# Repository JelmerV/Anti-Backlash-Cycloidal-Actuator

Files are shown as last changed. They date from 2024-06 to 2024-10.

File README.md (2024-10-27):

# MSc Thesis - Cost-Effective and Torque-Dense Cycloidal Actuator with Anti-Backlash Mechanisms

Accompaning files for the thesis work "Anti-Backlash Mechanisms for Cost-Effective Cycloidal Drive Robotic Actuators: Design and Evaluation"

Results - Test scripts - CAD source - Step files - Documentation - Diagrams - Photos

## Abstract

3D-printing is a promising method for cost-effective actuator designs, but it often results in less precise tolerances, leading to increased play.
In this work, we propose two novel anti-backlash mechanisms for cycloidal reducers. One uses a conically shaped cycloidal disk, and the other uses a split non-pinwheel design. Both were integrated into a compact actuator design. Two prototypes were manufactured and extensively tested in comparison to a baseline model. Experimental results show that the proposed mechanisms reduce play at the cost of increased friction. Both mechanisms utilize an adjustable preload that can be configured for the intended application based on the trade-off between play and friction.
Furthermore, the designed actuator demonstrates performance that is competitive with recent works. Using 3D-printed components proves to be a viable manufacturing method for cost-efficient designs.

## Actuator design

Baseline section views

<p float="left">
  Prototype parts
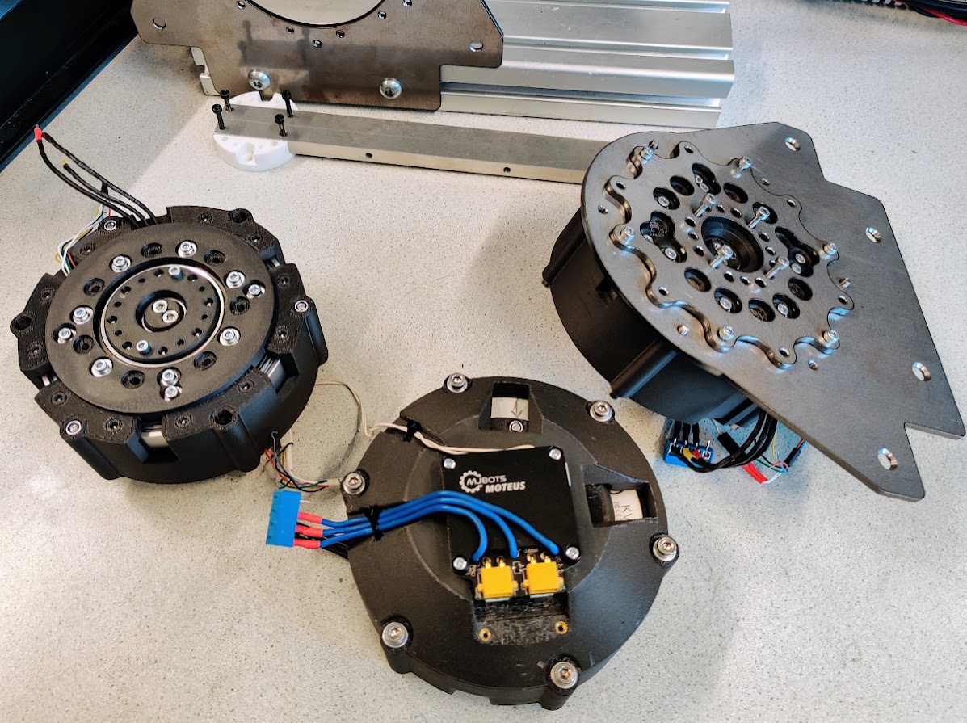
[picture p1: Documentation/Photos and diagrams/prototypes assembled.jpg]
Three assembled prototypes and mounting and locking plates
  
</p>

## Anti-Backlash mechanism

<p float="left">
    Split Non-pinwheel mechanism - modified parts
    Conic Cycloidal disk mechanism - modified parts
</p>

## File overview

`Agendas` All meeting agendas

`CAD Export` Exported CAD files, such as STEP files of the assemblies and individuald STL or STEP parts for 3D-printing

`CAD Source` SOLIDWORKS files of all components for easy modification

`CAD Source/test setup` SOLIDWORKS files for parts related to the tests and test setup

`CAD Source/off-the-shelf` SOLIDWORKS files for sourced parts, such as bearings and hardware

`Cycloid and Non-Pinwheel Profile Generation` Jupyter notebook file with scripts for the generation of cycloidal and non-pinwheel profiles. Included function to export (part of) the profile to DXF.

`Documentation` Files for some of the tables and comparisons of the paper

`Documentation/diagrams` SVG files of all diagrams and annotated images

`Documentation/CAD Section Views` Screenshots of the CAD design

`Documentation/Cad animations` Videos of the motions and exploded views of the CAD design

`Documentation/All photos and videos` All pictures and photos from the timeline of the project. All files are timestamped, so recorded tests can e matched by video and raw data

`Test Scripts` More details about these scripts in [corresponding README](<Test Scripts/README.md>)

`Test Scripts/test_data` Resulting test data, all files have timestamps and short descriptions in the name. All of the used data is aready added in the analysing notebook files

`Test Scripts/figures` Resulting plots as SVG files from the analysis notebooks

## License

Shield: [][cc-by-sa]

This work is licensed under a
[Creative Commons Attribution-ShareAlike 4.0 International License][cc-by-sa].

[][cc-by-sa]

[cc-by-sa]: http://creativecommons.org/licenses/by-sa/4.0/
[cc-by-sa-image]: https://licensebuttons.net/l/by-sa/4.0/88x31.png
[cc-by-sa-shield]: https://img.shields.io/badge/License-CC%20BY--SA%204.0-lightgrey.svg

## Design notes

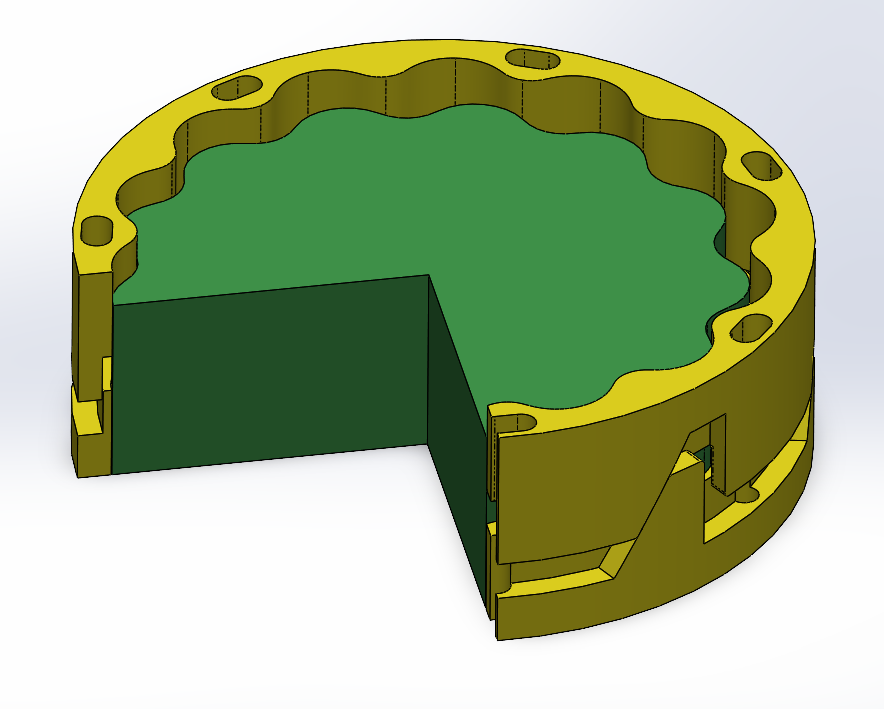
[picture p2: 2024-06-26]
Documentation/Preloading Concept Exploration/split pinwheel.png

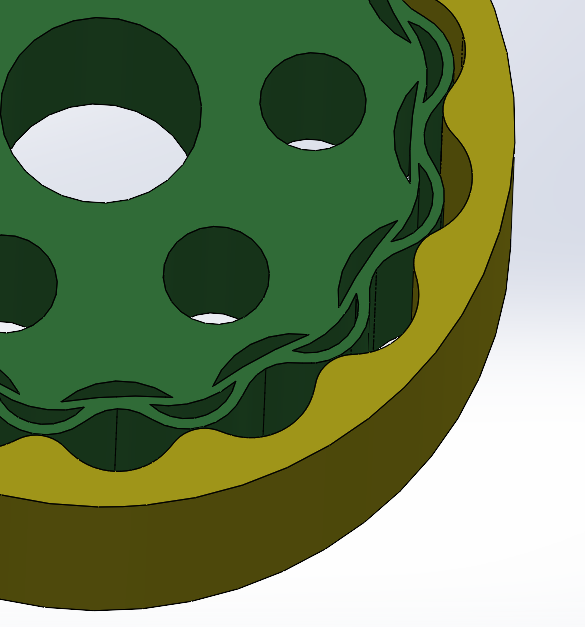
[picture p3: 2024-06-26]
Documentation/Preloading Concept Exploration/spring teeth disk close-up.png

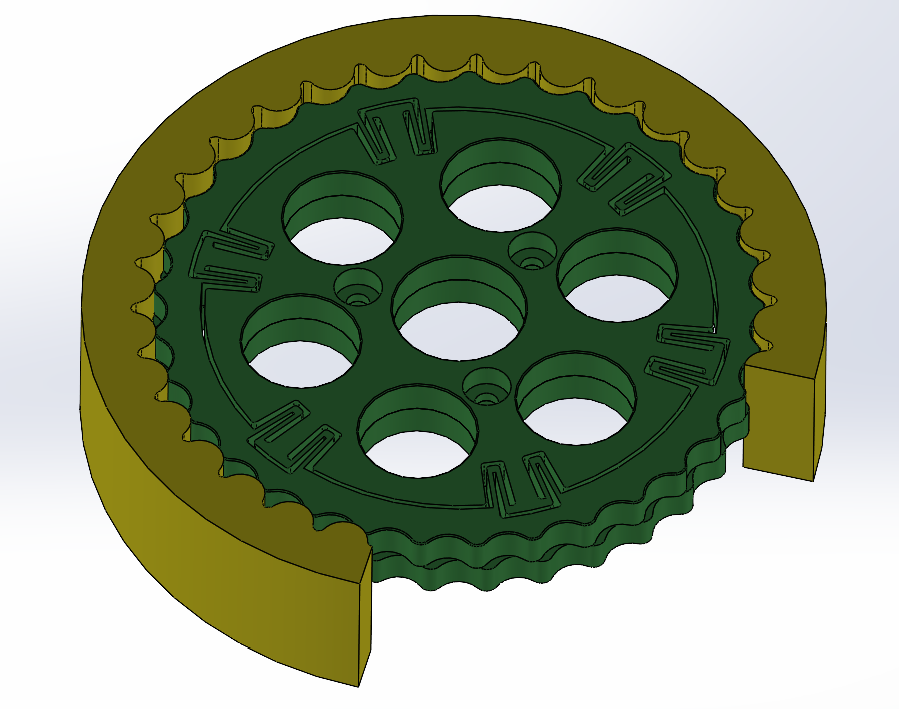
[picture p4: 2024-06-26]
Documentation/Preloading Concept Exploration/split disk flexure - sectioned.png

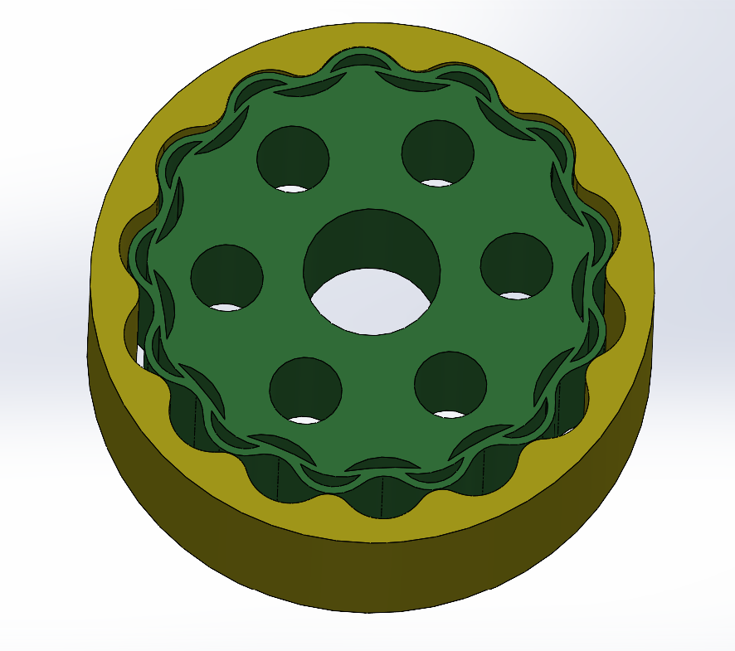
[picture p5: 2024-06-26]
Documentation/Preloading Concept Exploration/spring teeth disk.png

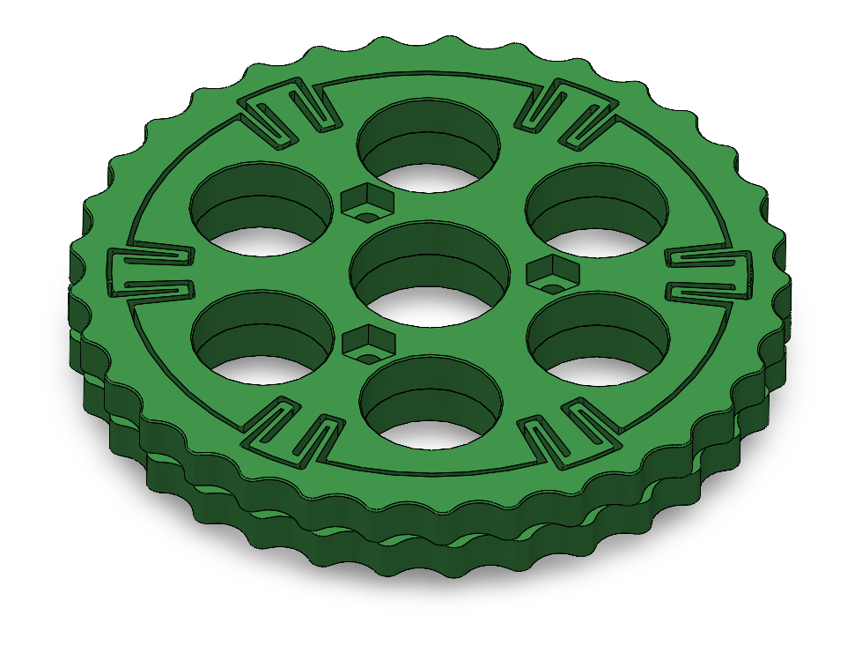
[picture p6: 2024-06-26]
Documentation/Preloading Concept Exploration/split disk flexures.png

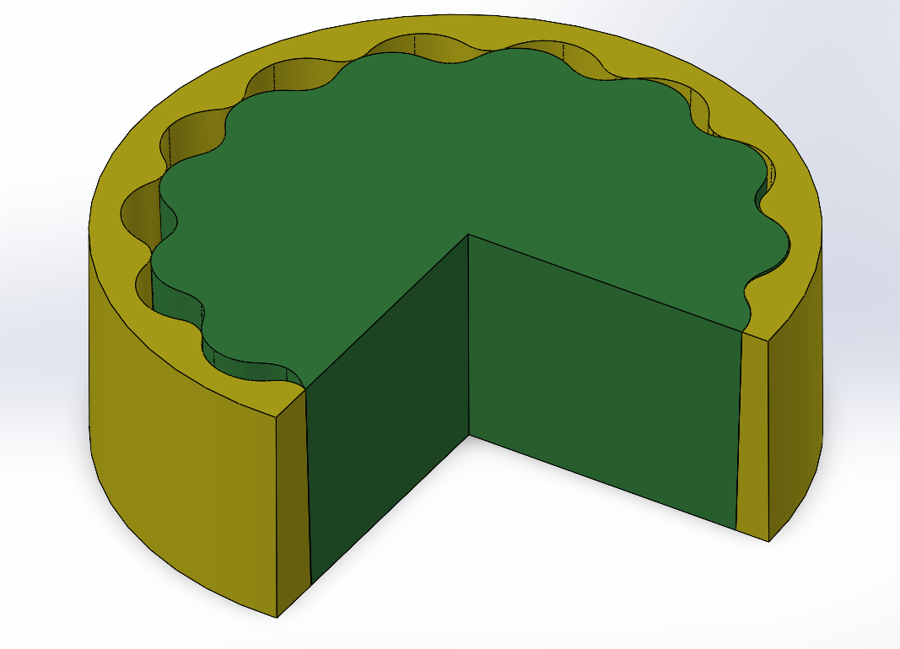
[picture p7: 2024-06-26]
Documentation/Preloading Concept Exploration/conic - sectioned.png

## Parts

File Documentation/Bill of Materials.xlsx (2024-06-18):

Kugellager express
Item | price | amount | total | link | Notes
6710 (50x62x6) | 9.95 | 10 | 99.5 | https://www.kugellager-express.de/deep-groove-ball-bearing-6710-61710-2rs-50x62x6-mm
6803 (17x26x5) | 1.39 | 5 | 6.95 | https://www.kugellager-express.de/deep-groove-ball-bearing-6803-61803-2rs-17x26x5-mm
6806 (30x42x7 | 2.89 | 4 | 11.56 | https://www.kugellager-express.de/deep-groove-ball-bearing-6806-61806-2rs-30x42x7-mm
HK 0509 | 0.71 | 100 | 71 | https://www.kugellager-express.de/drawn-cup-needle-roller-bearing-hk0509-open-hk0509-5x9x9-mm
HK 1522 | 2.84 | 4 | 11.36 | https://www.kugellager-express.de/drawn-cup-needle-roller-bearing-hk1522-open-hk1522-15x21x22-mm
IR 12x15x22.5 | 3.28 | 4 | 13.12 | https://www.kugellager-express.de/inner-ring-ir12x15x22-5-12x15x22-5-mm
total |  |  | 213.49
 |  |  |  |  |  | per actuator | total
DIN912 - M2.5x10 |  |  |  | at ram stock |  | 4 | 16
DIN912 - M2.5x35 |  |  |  |  |  | 7 | 14 | https://www.conrad.nl/nl/p/toolcraft-to-5358816-cilinderschroeven-m2-5-35-mm-sleuf-rvs-a2-1000-stuk-s-1786272.html | https://www.rwproducts.nl/din-912-cilinderschroef-binnenzeskant-rvs-a4-m2-5x35 | https://www.fabory.com/nl/cilinderschroef-met-binnenzeskant-din-912-roestvaststaal-%28rvs%29-a4-70-m2%2C5x35/p/55050025035
DIN912 - M3x6 |  |  |  | at ram stock |  | 10 | 40
DIN912 - M3x8 |  |  |  | at ram stock |  | 8 | 32
DIN912 - M3x12 |  |  |  | at ram stock |  | 7 | 28
DIN912 - M4x50 |  |  |  |  |  | 8 | 32
Countersink M4x10 |  |  |  |  |  | 10 | 40
Locknut M2.5 |  |  |  | at ram stock |  | 7 | 14
Locknut M3 |  |  |  | at ram stock |  | 26 | 104
Locknut M4 |  |  |  |  |  | 14 | 56
Washer M3 |  |  |  | at ram stock |  | 7 | 28
Washer M4 |  |  |  |  |  |  | 0
Large Washer M3 |  |  |  |  |  | 24 | 96
Large Washer M4 |  |  |  |  |  |  | 0
Fabory
DIN7979 Parallel pin with internal thread 5x45 (part nr. 39090.050.045) |  | 50 | 87 | https://www.fabory.com/nl/cilindrische-pen-met-binnendraad%2c-gehard%2c-geslepen-din-7979-d-staal-60%c2%b12hrc-blank-5x45mm/p/39090050045 | minimum quantity of 50. Need 40
AlcoMex Springs
Golfring W61460 | 3.15 | 5 | 15.75 | https://webshop.alcomex.nl/golfring-w61460
Schotelveer S22000 | 0.6 | 50 | 30 | https://webshop.alcomex.nl/schotelveer-8x3-2x0-3-s22000
total |  |  | 45.75
TinyTronics
Heat set inserts M2.5x5 (20pcs pack) | 2.5 | 1 | 2.5 | https://www.tinytronics.nl/en/tools-and-mounting/installation-and-mounting-material/threaded-inserts/threaded-insert-m2.5-5.0mm-20-pieces
Heat set inserts M3x5.7 (20pcs pack) | 2.75 | 2 | 5.5 | https://www.tinytronics.nl/en/tools-and-mounting/installation-and-mounting-material/threaded-inserts/threaded-insert-m3-5.7mm-20-pieces
Heat set inserts M4x5.8 (20pcs pack) | 3 | 1 | 3 | https://www.tinytronics.nl/en/tools-and-mounting/installation-and-mounting-material/threaded-inserts/threaded-insert-m4-5.8mm-20-pieces
Glue (metal to plastic)

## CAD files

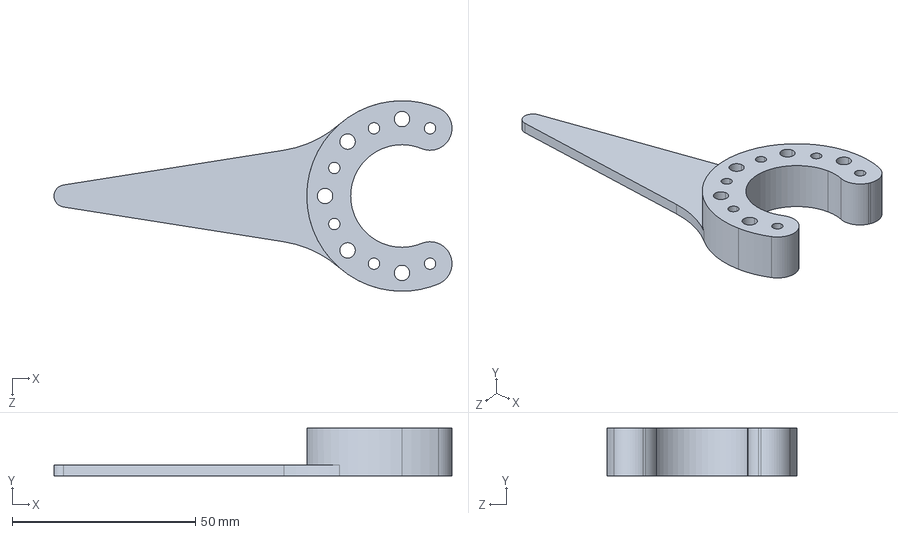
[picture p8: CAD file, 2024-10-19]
CAD Export/Output pointer.STEP
108.6 x 13.0 x 52.0 mm

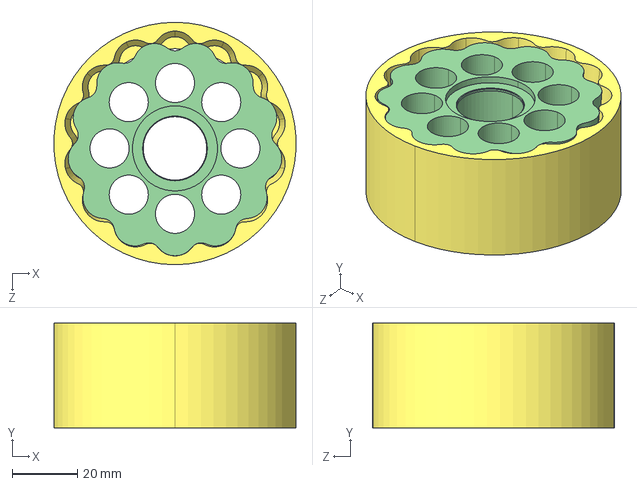
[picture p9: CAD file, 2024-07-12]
CAD Export/reducer parts V1.6/Cycloid Imported - Conic v1.6.STEP
74.0 x 32.0 x 74.1 mm

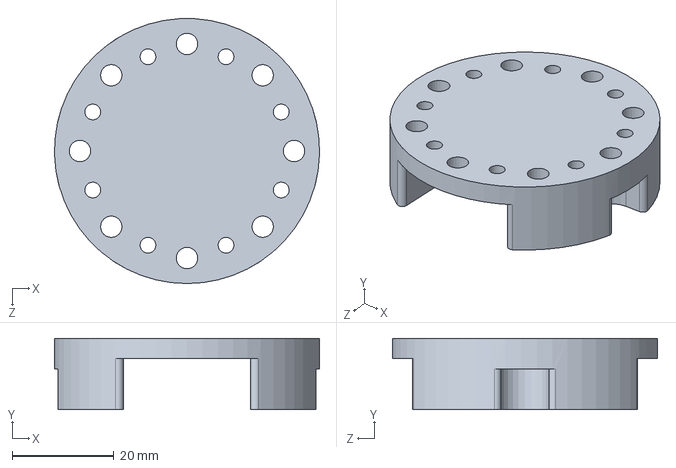
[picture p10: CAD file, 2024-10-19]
CAD Source/test setup/pendulum bar spacer.SLDPRT
52.0 x 14.0 x 52.0 mm

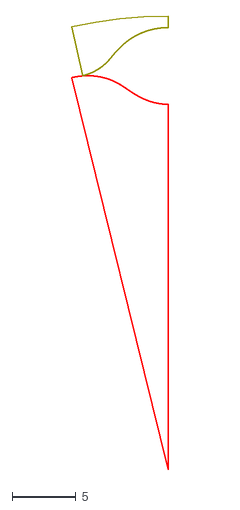
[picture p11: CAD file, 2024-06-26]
Cycloid and Non-Pinwheel Profile Generation/cycloid_N14_R34_Rr3.9_E1.5.dxf
7.57 x 35.5

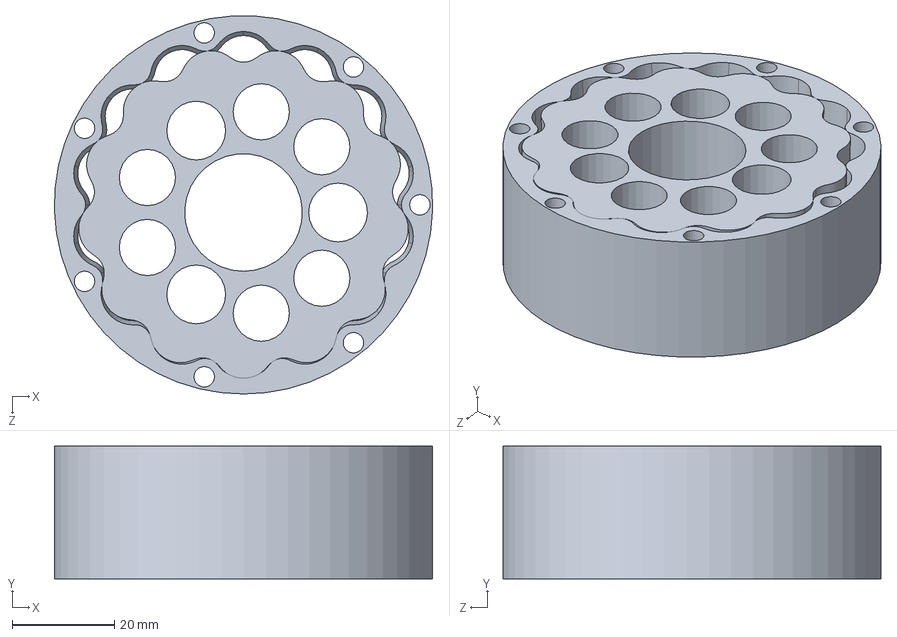
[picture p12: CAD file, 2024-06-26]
Documentation/Preloading Concept Exploration/conic cycloid import.SLDPRT
74.0 x 26.0 x 73.9 mm

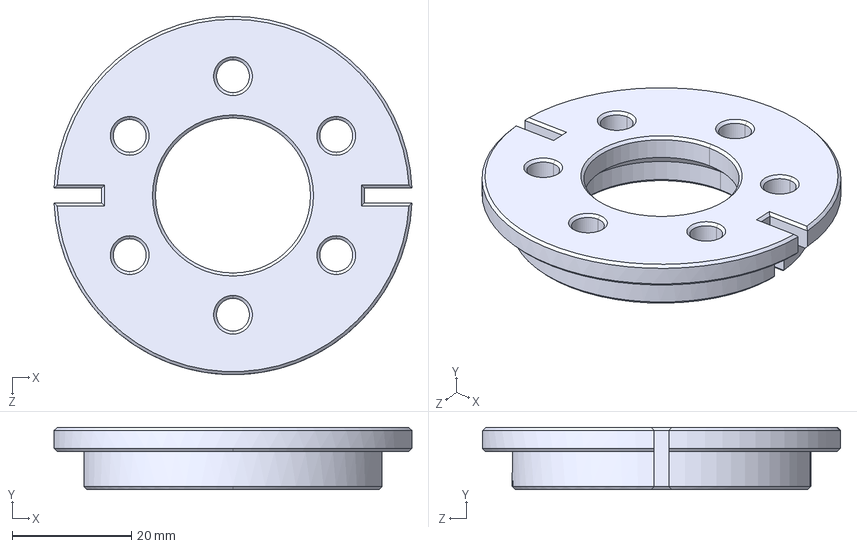
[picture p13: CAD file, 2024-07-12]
CAD Export/Rotor positioning tool.STEP
60.0 x 10.4 x 60.1 mm

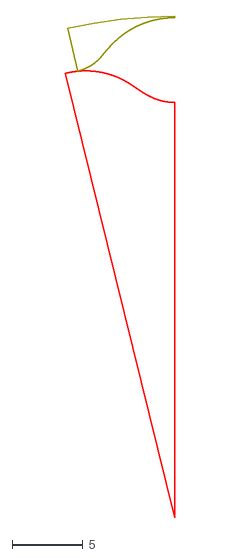
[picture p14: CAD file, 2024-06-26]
Cycloid and Non-Pinwheel Profile Generation/cycloid_N14_R34_Rr3.1_E1.5.dxf
7.75 x 35.5

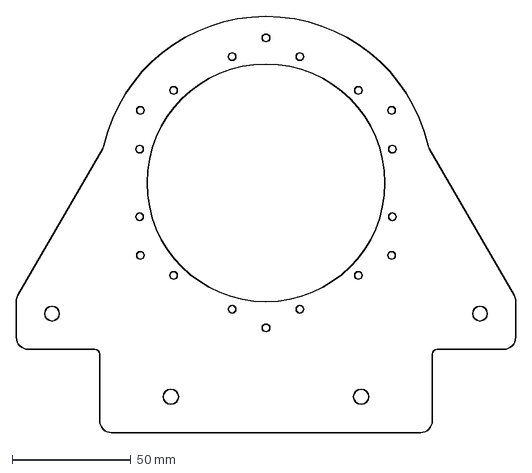
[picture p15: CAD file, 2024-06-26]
CAD Export/Actuator Mounting Plate.DXF
210.0 x 175.0 mm

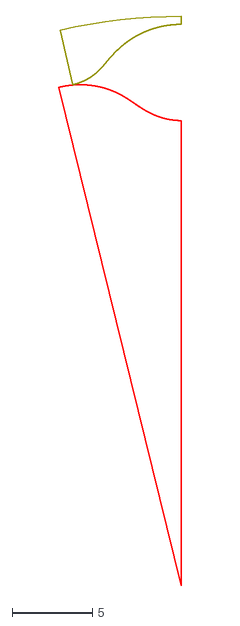
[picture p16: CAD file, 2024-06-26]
Cycloid and Non-Pinwheel Profile Generation/cycloid_N14_R34_Rr3.5_E1.5.dxf
7.66 x 35.5

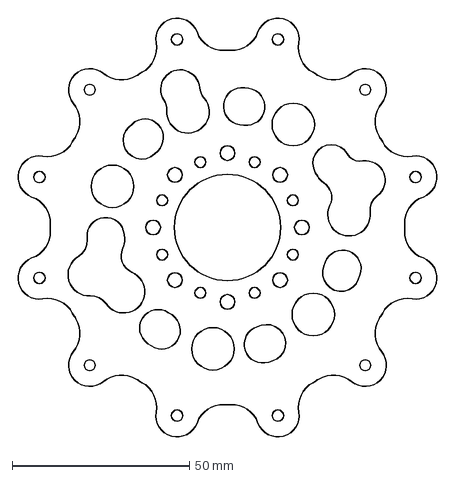
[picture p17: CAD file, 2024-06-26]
CAD Export/Output Fixing Plate.DXF
119.4 x 119.4 mm

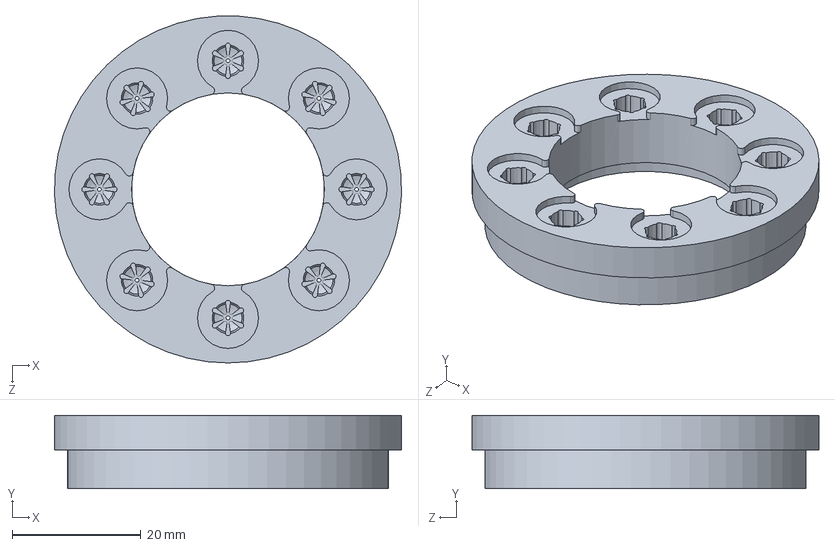
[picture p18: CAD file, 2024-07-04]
CAD source/Output Stiffener.SLDPRT
54.0 x 11.4 x 54.0 mm

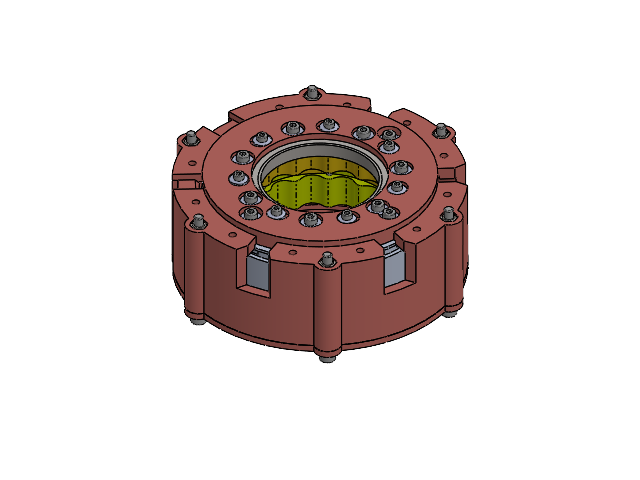
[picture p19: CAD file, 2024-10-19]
CAD source/Housing and Fixed parts.SLDASM
Housing base
Housing cap
RO100 - windings
RO100 - stator
RO100 - windings bottom
Cycloid Imported - Split Pinwheel
Ball Bearing Deep Groove
Moteus-r411-mechanical
Plain Washers x 16
Hex Socket Screw (DIN912) x 20
Locknut (DIN985) x 17
Heat Set Insert x 13
cable strain relief

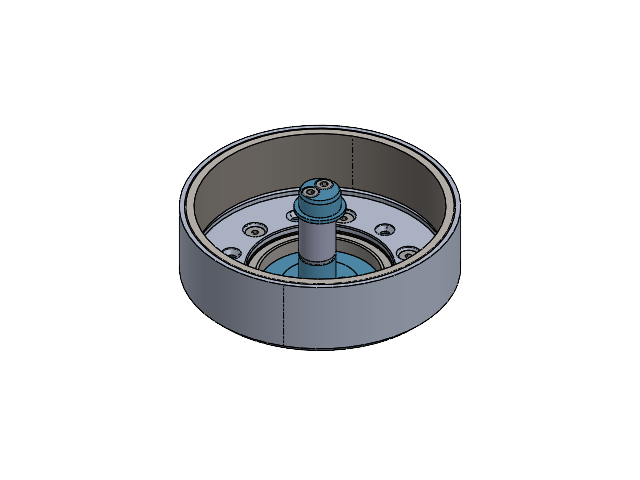
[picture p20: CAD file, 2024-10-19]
CAD source/Eccentric Shaft assem.SLDASM
Eccentric Shaft x 3
RO100 - rotor
RO100 - magnets
Ball Bearing Deep Groove x 2
Hex Socket Screw (DIN912) x 8
Shaft Liner IR_12x15x22.5
Moteus Diametric Sense Magnet
Locknut (DIN985) x 18
Preloading Ring x 2
Wave Disc Spring x 2
Hex Socket Screw Countersunk (DIN7991) x 6

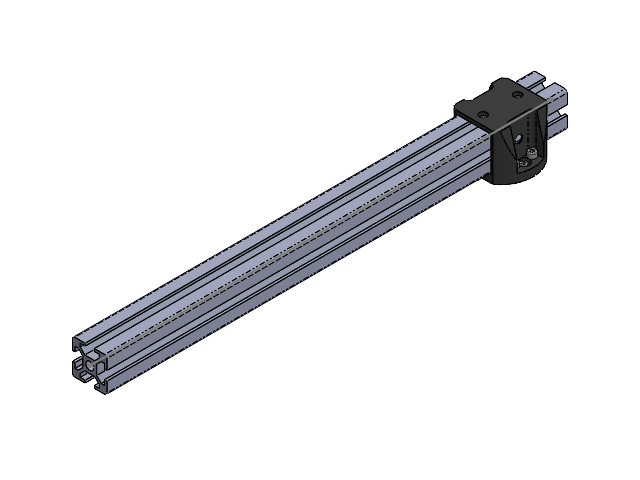
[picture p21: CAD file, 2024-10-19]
CAD source/Test setup/Pendulum.SLDASM
Output extrusion mount
Hex Socket Screw (DIN912) x 8
Plain Washers x 4
pendulum link

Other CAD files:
CAD source/Output Structure.SLDASM
CAD source/Cycloidal Disk assem.SLDASM
CAD source/Test setup/test base.SLDASM
CAD Source/test setup/Output pointer.SLDPRT
CAD Export/Output pointer.STL
CAD source/Eccentric Shaft.SLDPRT
CAD source/Housing base.SLDPRT
CAD source/Housing cap.SLDPRT
CAD source/Output Ring.SLDPRT
CAD source/Preloading Ring.SLDPRT
CAD source/Test setup/ATI Mini40 mount.SLDPRT
CAD source/Test setup/Actuator Mount print.SLDPRT
CAD source/Test setup/Actuator Mounting Plate.SLDPRT
CAD source/Test setup/Ati Mini40.SLDPRT
CAD source/Test setup/Output extrusion mount.SLDPRT
CAD source/Test setup/motor testing Shaft.SLDPRT
CAD source/Test setup/output fixing plate.SLDPRT
CAD source/Test setup/pendulum link.SLDPRT
CAD source/Test setup/testbed.SLDPRT
CAD source/cable strain relief.SLDPRT
CAD source/off-the-shelf/3030 corner bracket.SLDPRT
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

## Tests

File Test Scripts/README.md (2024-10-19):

# Script details:

## Test scripts:

These scripts require the moteus python library, installed via `pip3 install moteus`. See the [python reference](https://github.com/mjbots/moteus/blob/main/lib/python/README.md) and the  [full Moteus reference](https://github.com/mjbots/moteus/blob/main/docs/reference.md) for details.

`actuator.py` Shared abstraction layer for the moteus motor controller using the USB to canFD interface. Used by all other test scripts

`record_max_torque.py` torque ramps with configurable duration and peak

`record_speedramp.py` Speed ramp with configurable duration and peak

`record_torque_constant.py` Torque ramp in combination with a mini40 loadcell (untested)

`record_torqueramp.py` Torque ramps for play and stiffness. multiple repetations at 2 different peaks. Used for play and stiffness estimation

`record_trajectory.py` For a trajectory of postions with configurable speed limit. Repeats trajectory at increasing accelerations.

`record-run-in.py`  Run actuator in alternating directions indefinetly while saving CSV data.

## Data processing scripts

These files are jupyter notebook files requiring the jupyter python library, or can be opened using vs-code. Furthermore, they require some libraries installed by `pip install numpy matplotlib pandas`

`analyse_anti-backlash.ipynb` jupyter notebook for the play, stiffness, and friction tests and all resulting plots. Saved plots as SVG are the ones used in the the paper.

`analyse_performance.ipynb` jupyter notebook for the maximum torque and velocity tests and plots, as well as the pendulum trajectory tracking tests and corresponding plots

## Directory

`./test_data` Resulting test data, all files have timestamps and short descriptions in the name. All of the used data is aready added in the analysing notebook files

`./figures` Resulting plots as SVG files from the analysis notebooks

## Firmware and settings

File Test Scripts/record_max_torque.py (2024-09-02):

'''
Do a slow torque ramp towards a small position change. Used to estimate internal play and stiffness
'''

import time, datetime
import math

import numpy as np
import pandas as pd
import matplotlib.pyplot as plt
import threading

import asyncio
from actuator import Actuator

abs_start_time = time.monotonic_ns()
e_stop = False

async def do_torque_ramp(actuator: Actuator, duration, max_torque):
    # ramp up till max torque in either direction 
    ramp_duration = duration/2

    states = []
    succes = True

    try:
        print(f'Ramping to {max_torque} Nm in {ramp_duration} seconds.', end=' ', flush=True)
        start_time = time.monotonic_ns()
        while not e_stop:
            pct_done = (time.monotonic_ns() - start_time) / (ramp_duration*1e9)
            if pct_done > 1.0:
                break
            torque = max_torque * pct_done
            result = await actuator.set_position(feedforward_torque=torque, kp_scale=0.0, kd_scale=0.0, velocity_limit=0.5)
            states.append(actuator.state_to_dict(result, time.monotonic_ns()))
            await asyncio.sleep(0.001)
            
        if states[-1]['FAULT'] != 0:
            print(f'fault code: {states[-1]["FAULT"]}, STOPPING')
            raise Exception('Fault detected')

        #ramp down torque
        print(f'\tand back down', end=' ', flush=True)
        start_time = time.monotonic_ns()
        while not e_stop:
            pct_done = (time.monotonic_ns() - start_time) / (ramp_duration*1e9)
            if pct_done > 1.0:
                break
            torque = max_torque * (1-pct_done)
            result = await actuator.set_position(feedforward_torque=torque, kp_scale=0.0, kd_scale=0.0, velocity_limit=0.02)
            states.append(actuator.state_to_dict(result, time.monotonic_ns()))
            await asyncio.sleep(0.001)

    except Exception as e:
        print(f'torqueramp failed. Error: {e}')
        succes = False

    finally:
        if e_stop:
            print(f'Emergency stop detected, stopping motor')
            succes = False
        print(f'\tDone. stopping motor')
        # await actuator.m.set_stop()
            
        return succes, states
    

def torque_ramp_test(actuator: Actuator, test_duration, max_torque):
    ramp_duration = test_duration/2
    pos_succes, pos_states = asyncio.run(do_torque_ramp(actuator, ramp_duration, max_torque))
    test_df = pd.DataFrame(pos_states)
    if pos_succes:
        neg_succes, neg_states = asyncio.run(do_torque_ramp(actuator, ramp_duration, -max_torque))
        test_df = pd.concat([test_df, pd.DataFrame(neg_states)])
    
    if not pos_succes or not neg_succes:
        asyncio.run(actuator.m.set_stop())
        asyncio.run(actuator.set_position_bounds('nan', 'nan'))

        timestamp = datetime.datetime.now().strftime('%Y-%m-%d__%H-%M-%S')
        filename = f'test_data/{timestamp}__torquerampfailed__{test_name}.csv'
        test_df.to_csv(filename, index=False)

        print(f'Ramp failed, still saved data to {filename}')
        test_df.plot(x='TIME', y='TORQUE')
        plt.show()
        exit()
        
    # test_df['TORQUE_smooth'] = test_df['TORQUE'].rolling(window=20, center=True).mean()
    return test_df


def e_stop_detector():
    global e_stop
    while True:
        inp = input('type q to stop: ')
        if inp == 'q':
            e_stop = True
            break
        time.sleep(0.05)
    


if __name__ == '__main__':
    STIFFNESS_TEST_TORQUE = 90.0          # Nm at output
    STIFFNESS_TEST_DURATION = 8.0
    STIFFNESS_TEST_REPETITIONS = 2

    # STORED_DATA = ['POSITION', 'TORQUE', 'CONTROL_TORQUE', 'Q_CURRENT', 'FAULT', 
    STORED_DATA = [ 'POSITION', 'TORQUE', 'CONTROL_TORQUE', 'Q_CURRENT',
                    'FAULT', 'TRAJECTORY_COMPLETE',
                    'TEMPERATURE', 'MOTOR_TEMPERATURE',
    ]


    print('\nStarting torque ramp test')
    print(f'torque test: {STIFFNESS_TEST_TORQUE}Nm, {STIFFNESS_TEST_DURATION}s, {STIFFNESS_TEST_REPETITIONS} repetitions')
    print('')
    test_name = input('Enter test name: ')

    if test_name == '':
        print('No test name given, exiting')
        exit()


    # initialize actuator
    actuator = Actuator(actuator_id=1, stored_data=STORED_DATA)

    # set position to zero
    asyncio.run(actuator.m.set_output_nearest(position=0.0))

    #for safety, configure motion limits
    MAX_DEVIATION = 0.3    # measured in output revolutions    
    result = asyncio.run(actuator.set_position())
    asyncio.run(actuator.m.set_stop())
    cur_pos = actuator.state_to_dict(result)['POSITION']
    print(f'Current position: {cur_pos}, setting bounds to {cur_pos-MAX_DEVIATION} to {cur_pos+MAX_DEVIATION}')
    asyncio.run(actuator.set_position_bounds(cur_pos-MAX_DEVIATION, cur_pos+MAX_DEVIATION))


    #start emergency stop
    e_stop_thread = threading.Thread(target=e_stop_detector, daemon=True)
    e_stop_thread.start()


    # move to a repeatable position:
    succes, states = asyncio.run(do_torque_ramp(actuator, duration=2.0, max_torque=-3.0))
    if not succes:
        print('Failed to move to repeatable position, is output fixed?')
        exit()

    print('Starting tests\n')
    abs_start_time = time.monotonic_ns()
    all_states = []

    for i in range(STIFFNESS_TEST_REPETITIONS):
        test_df = torque_ramp_test(actuator, test_duration=STIFFNESS_TEST_DURATION, max_torque=STIFFNESS_TEST_TORQUE)
        test_df['test_nr'] = i+100
        all_states.append(test_df)
        print(f'large ramp ramp {i} done')
        

    # stop and restore old bounds config
    asyncio.run(actuator.m.set_stop())
    asyncio.run(actuator.set_position_bounds('nan', 'nan'))


    # store the data
    df = pd.concat(all_states)
    df['TIME'] = (df['TIME'] - abs_start_time) / 1e9

    timestamp = datetime.datetime.now().strftime('%Y-%m-%d__%H-%M-%S')
    filename = f'test_data/{timestamp}__torqueramp__{test_name}.csv'
    print(f'Test done succesful. Saving to {filename}')
    df.to_csv(filename, index=False)


    df['MOTOR_TEMPERATURE'] = df['MOTOR_TEMPERATURE'] * 0.442 - 1.62

    # plot
    fig, ax = plt.subplots(4, 1, figsize=(10, 14), sharex=True)
    df.plot(x='TIME', y=['POSITION'], ax=ax[0])
    df.plot(x='TIME', y=['TORQUE', 'CONTROL_TORQUE'], ax=ax[1])
    df.plot(x='TIME', y=['Q_CURRENT'], ax=ax[2])
    df.plot(x='TIME', y=['TEMPERATURE', 'MOTOR_TEMPERATURE'], ax=ax[3])

    plt.show()
    
    print('Done')

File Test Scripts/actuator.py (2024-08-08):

import math
import asyncio
import moteus
import time


STORED_DATA = {
    'POSITION',  'COMMAND_POSITION', 'CONTROL_POSITION',
    'VELOCITY', 'COMMAND_VELOCITY', 'CONTROL_VELOCITY',
    'TORQUE', 'Q_CURRENT'
}


class Actuator:
    def __init__(self, actuator_id=1, stored_data=STORED_DATA, qr=None):
        self.stored_data = stored_data
        self.m = self.start_actuator(actuator_id)
        self.s = moteus.Stream(self.m, verbose=True)

        asyncio.run(self.store_old_config())


    def prep_query_resolution(self, stored_data=None):
        if stored_data is None:
            stored_data = self.stored_data.copy()

        qr = moteus.QueryResolution()

        if 'TRAJECTORY_COMPLETE' in stored_data:
            qr.trajectory_complete = moteus.INT8            

        for attr in dir(qr):
            if attr.startswith('_'):
                continue
            if attr.upper() in stored_data:
                if getattr(qr, attr) == moteus.IGNORE:
                    setattr(qr, attr, moteus.F32)
                stored_data.remove(attr.upper())
            else:
                setattr(qr, attr, moteus.IGNORE)

        for register in stored_data:
            qr._extra[moteus.Register[register]] = moteus.F32

        return qr

    def start_actuator(self, actuator_id):
        qr = self.prep_query_resolution()
        m = moteus.Controller(id=actuator_id, query_resolution=qr)
        asyncio.run(m.set_stop())      

        return m
    
    async def set_position(self, position=math.nan, velocity=math.nan, **kwargs):
        results = await self.m.set_position(
            position=position,
            velocity=velocity,
            **kwargs,
            query=True,
        )
        return results
    
    async def slow_down(self):
        await self.m.set_position_wait_complete(
            position=math.nan,
            velocity=0.0,
            accel_limit=10.0,
        )
    
    async def stop_and_zero(self):
        await self.m.set_stop()
        await asyncio.sleep(0.05)
        await self.m.set_output_nearest(position=0.0)

    async def store_old_config(self):
        await self.s.write_message(b"tel stop")
        await self.s.flush_read()
        await self.s.command(b"d stop")

        self.old_position_min = await self.read_config_double("servopos.position_min")
        self.old_position_max = await self.read_config_double("servopos.position_max")


    async def read_config_double(self, name):
        response = await self.s.command(f"conf get {name}".encode('utf8'), allow_any_response=True)
        return float(response.decode('utf8'))
    
    async def set_position_bounds(self, upper=None, lower=None):
        upper = upper or self.old_position_max
        lower = lower or self.old_position_min

        await self.s.command(f'conf set servopos.position_min {upper}'.encode('utf8'))
        await self.s.command(f'conf set servopos.position_max {lower}'.encode('utf8'))
        await self.s.command(f'conf write'.encode('utf8'))
        
    def state_to_dict(self, state, timestamp=None):
        state_dict = {'TIME': timestamp or time.time()}
        for register in self.stored_data:
            state_dict[register] = state.values[moteus.Register[register]]
        return state_dict

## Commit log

2024-06-18 Initial commit
    CAD V1.5 and early testing code
    [3030 corner bracket.SLDPRT, Actuator Mount print.SLDPRT, Actuator Mounting Plate.SLDPRT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]
2024-06-26 cleanup
    updated test-setup and added step files
    [ATI Mini40 mount.SLDPRT, Actuator Mounting Plate.DXF, Ati Mini40.SLDPRT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]
2024-06-30 Added test data
    [2024-06-18_17-38-36_torqueramp_baseline.csv, 2024-06-27__14-15-42__torqueramp__conic init 1.csv, 2024-06-27__14-22-03__torqueramp__conic init 2.csv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]
2024-07-04 CAD tweaks (V1.6), run-in test scripts, new test_data
    [07-04_11-18-44_run-in_split pinwheel_0.5rps.csv, 07-04_11-31-57_run-in_split_0.5rps.csv, 07-04_11-32-24_run-in_split_0.5rps.csv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]
2024-07-12 improved scripts and new test data. CAD v1.6 with small tweaks
    [2024-07-08__10-39-20__torqueramp__conic init5.csv, 2024-07-08__10-45-19__torqueramp__conic init1.csv, 2024-07-08__10-51-07__torqueramp__conic init6.csv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]
2024-07-12 more testdata
    [2024-07-12__14-07-48__torqueramp__conic 1pre1.csv, 2024-07-12__14-26-23__torqueramp__conic 1pre5.csv, 2024-07-12__14-31-48__torqueramp__conic 1pre6.csv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]
2024-07-19 improved scripts, more data
    [2024-07-17__12-24-38__torqueramp__base910 reamed1.csv, 2024-07-17__12-40-35__torqueramp__base910 reamed5.csv, 2024-07-17__12-45-13__torqueramp__base910 reamed6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]
2024-07-27 new data
    [2024-07-19__13-27-30__torqueramp__conic_onyx 1pre1.csv, 2024-07-19__13-30-53__torqueramp__conic_onyx 1pre1.csv, 2024-07-19__13-37-48__torqueramp__conic_onyx 1p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]
2024-08-08 added torque test and trajectory moves
    [2024-08-06__12-02-58_speedramp_baseline onyx topspeed_100s.csv, 2024-08-06__14-52-13_trajectory_l.csv, 2024-08-06__14-55-05_trajectory_l.csv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]
2024-08-20 tweaked plots
    [Cycloidal Disk assem.SLDASM, Eccentric Shaft assem.SLDASM, Housing and Fixed parts.SLDASM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]
2024-08-23 files restructure and cleanup
    [07-04_11-18-44_run-in_split pinwheel_0.5rps.csv, 07-04_11-31-57_run-in_split_0.5rps.csv, 07-04_11-32-24_run-in_split_0.5rps.csv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]
2024-08-23 Improved readme and images
    [conic cycloid import.SLDPRT]
2024-08-25 cleaned up CAD
    [Actuator Mounting Plate.DXF, Baseline disk.STL, Conic non-pinwheel (-0.05).STEP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]
2024-08-26 small tweaks
    [Bill of Materials.xlsx, Cycloidal Disk assem.SLDASM, Housing and Fixed parts.SLDASM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]
2024-09-02 improved diagrams
    [Cycloidal Disk assem.SLDASM, Housing and Fixed parts.SLDASM, Output Structure.SLDASM]
2024-09-08 diagram tweaks
    [Housing and Fixed parts.SLDASM, Output Structure.SLDASM]
2024-10-19 improved documentation, last changes
    [Cycloidal Disk assem.SLDASM, Eccentric Shaft assem.SLDASM, Housing and Fixed parts.SLDASM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]
